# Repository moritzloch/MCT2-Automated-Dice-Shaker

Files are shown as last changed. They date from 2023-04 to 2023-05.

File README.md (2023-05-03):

# Automated Dice Shaker

***
Project for "Introduction to Microcomputers 2" by Marco Schweizer & Moritz Loch

&copy; 2023

***

## Konzept

Die Entwicklung des Konzeptes für dieses Projekt erfolgte mithilfe von ChatGPT und dem Prompt "Lustige Arduino Projekte". Die Idee eines automatisierten Würfelbechers wurde zum "Mäxle-Automat" erweitert, ein Automat der das beliebte Würfel-(Trink-)spiel spielen kann.
In der ursprünglichen Planung war angedacht, das automatisierte Würfeln durch eine rotierende Grundplatte zu realisieren. Der Würfel sollte durch den Drehimpuls gewürfelt werden. Zur Erkennung des Würfelergebnisses sollte ein Farbsensor die Farbe eines Farbwürfels registrieren.
Die folgende Skizze zeigt das ursprüngliche Konzept.

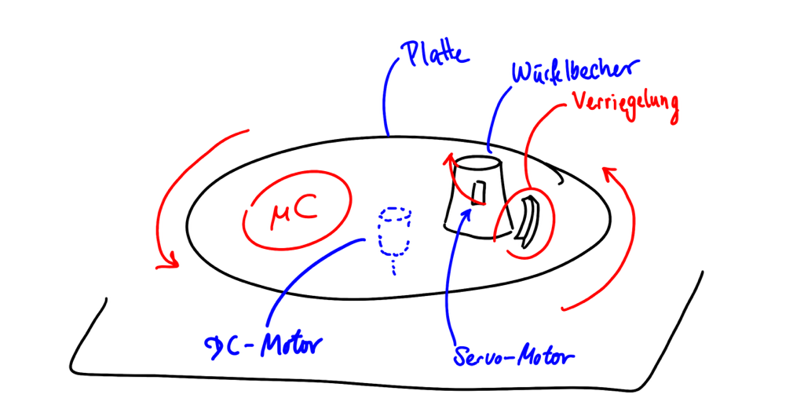
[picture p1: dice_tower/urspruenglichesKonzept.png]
Skizze des ursprüngliches Konzepts


Zu Beginn des Projektes zeigte sich, dass der TCS3200 Farbsensor nicht zuverlässig die Farbe des Farbwürfels identifizieren kann. Grund dafür ist unter anderem, dass keine gleichmäßige Belichtung des Würfels sichergestellt werden konnte und die Farben des Würfels im RGB-Farbspektrum zu nahe beieinander liegen, dass häufige Verwechslungen auftraten.
Deshalb wurde entschieden, Mäxle-Spiel und das Würfeln separat zu entwickeln. Beide Komponenten sind so aufeinander abgestimmt, dass eine zukünftige Zusammenführung problemlos ist. Für die notwendige Schnittstelle dazwischen, ist in Zukunft ein anderer Sensor zu Betrachten.

***

## Mäxle-Spiel

### Aufbau

Die Software zum Mäxle-Spiel umfasst eine Finite State Machine (FSM) mit 26 Zustände. Diese ermöglicht eine umfangreiche Menüsteuerung, sowie die Konfiguration und Durchführung von drei verschiedene Spielmodi. Die Informationsausgabe erfolgt mit einem 16x2 LCD-Display. Der Spieler kann durch Drehung eines Rotary Encoders Werte auswählen. Zustandsübergänge geschehen bei Knopfdruck des Rotary Encoders. Ein weiterer Knopf setzt den Zustandsautomaten zurück.
Beide Knöpfe sind Interruptgesteuert.
Die Hauptbedienelemente wurden zur komfortableren Handhabung in ein Bedientableau eingebettet.

### Programmablauf

Im Setup werden das LCD-Display initiiert, I/O deklariert und Interrupts angehängt. Außerdem werden die Menüs und Spieldaten zurückgesetzt.
Die Schleife fragt periodisch ab, ob eine der Interrupt-Flaggen gesetzt wurde. Der Encoder-Interrupt löst einen Übergang zum nächsten Zustand aus. Der Reset-Interrupt setzt das Spiel zurück. Andernfalls wird die, zum aktuellen Zustand zugehörige, Funktion ausgeführt.

Folgende Abbildung zeigt den vereinfachten [Programmablauf](/doc//Maexle_program_sequence.pdf).

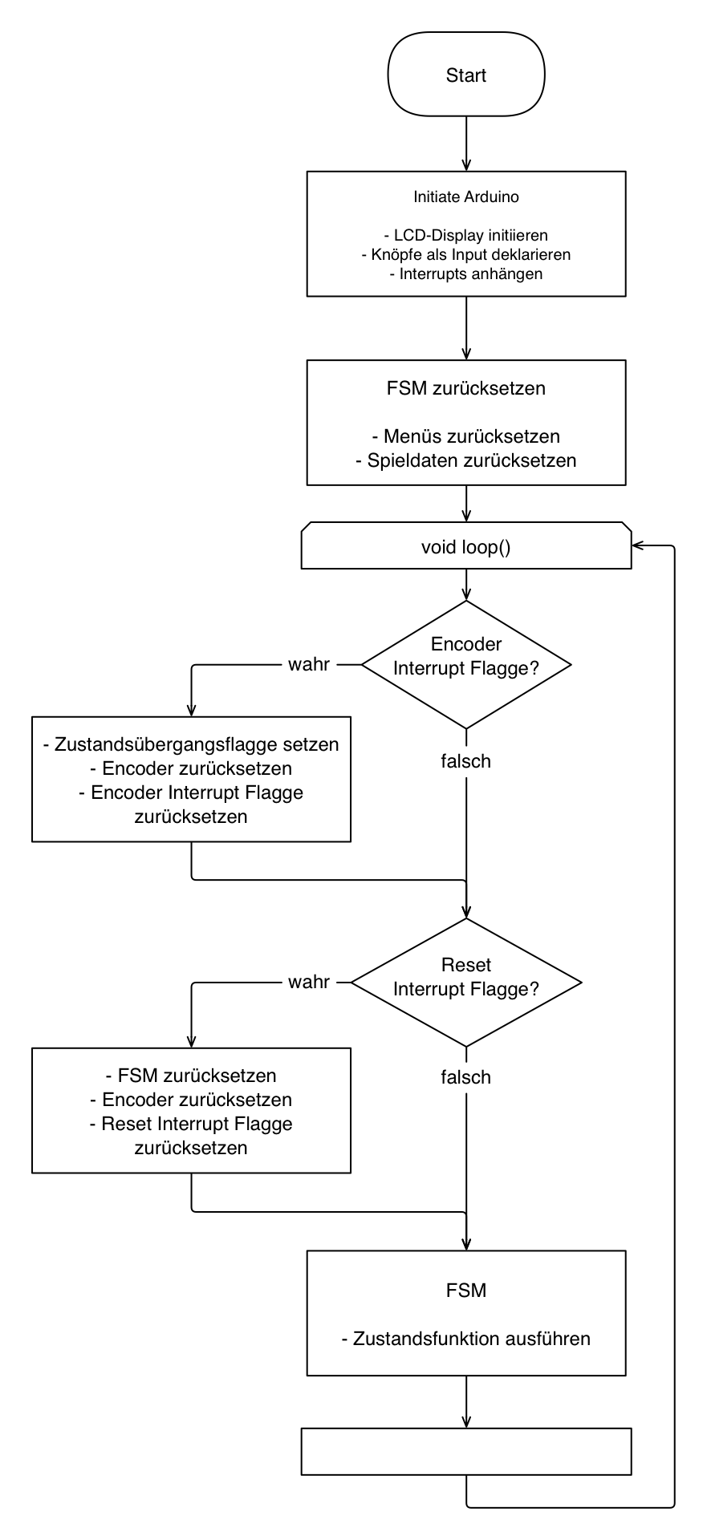
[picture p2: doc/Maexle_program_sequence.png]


### Zustandsautomat

Der Zustandsautomat ist durch ein Switch-Case-Statement implementiert. Dabei besitzt jeder Zustand eine eigene Funktion. In dieser ist sowohl die auszuführende Aktivität als auch der Übergang zum nächsten Zustand geregelt.

Ausgangspunkt des Programms bildet das Hauptmenü zur Auswahl der Spielmodi. Dieses und alle weiteren Scroll-Menüs sind als Funktion implementiert. Diese ermöglicht die Darstellung eines beliebigen Scroll-Menüs. Auch alle weiteren Displayausgaben sind als allgemeine Funktionen umgesetzt.

```c
/**
 * @brief Custom scroll selection menu on lcd display
 * 
 * @param menuProperties Menu from which the items will be selected
 * @param menuItemNames Names of the items in the menu
 * @param firstFrame First frame of FSM state flag
 * @return uint8_t 0
 */
uint8_t lcdScrollMenu(MenuProperties* menuProperties, const char** menuItemNames, bool* firstFrame)
```

Vom Hauptmenü aus gelangt der Spieler in die Nebenspielmodi "Würfeln" und "Noten würfeln". Beide können durch Einstellung der Würfel- und Augenzahl bzw. der maximalen Bestnote beliebig konfiguriert werden. Alle Spieleinstellungen und -daten werden in der folgenden Struktur gespeichert.

```c
/**
 * @brief Stores all current data of FSM
 * 
 */
struct FsmProperties{
    bool stateTransition = false;
    bool firstFrame = true;
    state_t currentState = ST_MENU;
    state_t nextState = ST_MENU;
    gameMode_t gameMode;

    int8_t numberOfLives;
    int8_t numberOfPlayers;
    uint8_t lifeCount[9];
    uint8_t currentPlayer;
    uint8_t nextPlayer;
    int8_t prevDiceRollIndex;
    int8_t diceRollIndex;
    bool trueNumberAnnounced;
    int8_t winningPlayer = -1;

    int8_t numberOfDice;
    int8_t numberOfEyes;

    float maxGrade = DEFAULTMAXGRADE;

    bool autoDiceRoll = DEFAULTAUTODICEROLL;
  };
  static FsmProperties fsm;
  ````

Anschließend liefert das Programm mit jedem Knopfdruck ein neues Würfelergebnis bzw. eine neue Note.

Bei Auswahl des Hauptspielmodus "Mäxle" kann der Spieler zunächst die Anzahl von Leben und die Anzahl der Spieler, die neben der CPU am Spiel teilnehmen wählen. Bei Spielbeginn wird zufällig ein Spieler ausgesucht, der beginnt.
Menschliche Spieler geben ihre Würfelsumme mittels Drehencoder ein. Die CPU würfelt pseudozufällig. Stattdessen kann zukünftig das automatisierte Würfeln mittels Würfelturm eingebunden werden.
Der nächste Spieler entscheidet anschließend mit einem Auswahlmenü ob er dem vorhergehenden Spieler glaubt oder nicht. Muss die CPU entscheiden, so tut sie das zufällig. Falls dem würfelnden Spieler nicht geglaubt wird muss dieser nun aufdecken, ob er tatsächlich gelogen hat. Andernfalls beginnt ein neuer Spielzug. Ist der würfelnde Spieler die CPU, dann wird dieser Schritt übersprungen. Zum Schluss wird dem lügenden oder dem falsch ratenden Spieler ein Leben abgezogen.
Ein abschließender Zustand überprüft ob das Spiel im vergangen Spielzug bereits gewonnen wurde und setzt die Spielzugdaten zurück. Falls das Spiel gewonnen wurde, wird der Sieger auf dem Display ausgegeben und das Spiel kehrt ins Hauptmenü zurück. Andernfalls beginnt der Spielzug des nächsten Spielers.

Der vollständige Zustandsautomat ist [hier](/doc/Maexle_State_Diagram.pdf) zu sehen.

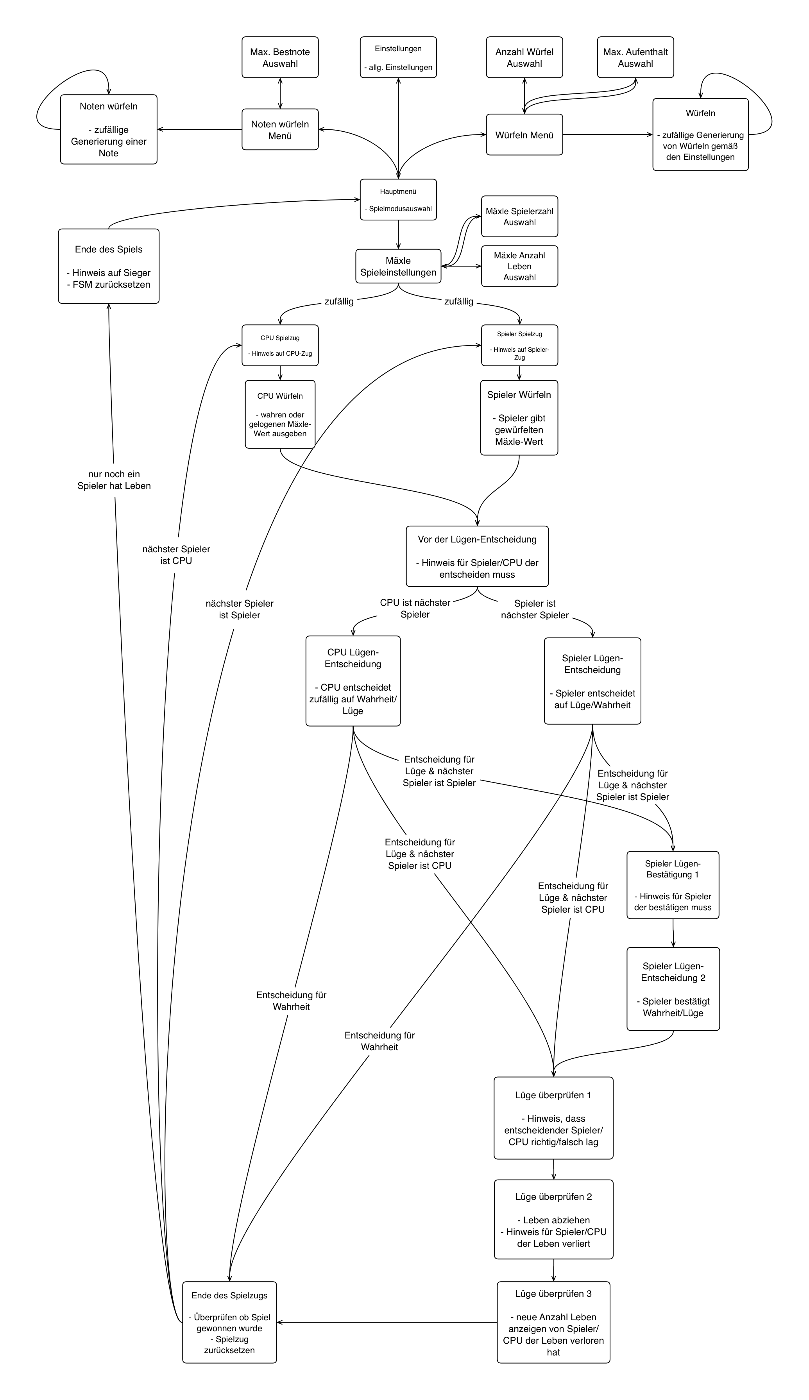
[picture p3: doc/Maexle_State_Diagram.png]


***

## Würfelturm

Neben den Bedien- und Anzeigeelementen (LCD-Display, Rotary Encoder und Taster), lag der Fokus vor allem auf dem halbautomatischem Würfelsystem.
Das ursprüngliche Konzept mit Farberkennung und rotierender Würfelfläche wurde nicht allein aufgrund des Sensors zugunsten der aktuellen Version verworfen, sondern auch bedingt einiger Probleme in der Hardware. Zum einen ist eine rotierende Platte der vorgesehenen Größe schwer zu realisieren, da der Aufbau komplex sein müsste um nicht (in anfänglichen Tests) aus der Balance zu geraten. Zum anderen sind Zweifel an der Umsetzbarkeit aufgekommen, da der Servo den Becher fest auf der Oberfläche halten soll, während die Platte mit einer hohen Drehzahl rotieren muss um den Würfel anzuheben.

Aufgrund dieser Punkte kam es zum Wechsel der Konzepte: Bestehend aus 2 Servos und einer Menge an [selbst entworfenen Bauteilen](/dice_tower/DiceShaker_Files) wurde ein System von Grund auf entwickelt, das mit einer Ausreichenden Zuverlässigkeit auf Anforderung selbstständig würfeln kann. Zukünftig kann die Ansteuerung des Mechanismus direkt durch das Programm des Mäxle-Spiels erfolgen.

Der Würfelturm besteht aus drei Bereichen: Dem Turm, dem Auffangbereich und dem Hubarm.
Der Turm besteht aus zwei schräg angeordneten Platten, welche den Würfel ablenken, wodurch dieser eine zufällige Flugbahn annimmt. Gespeißt wird er durch den Hubarm. Dieser wiederrum erhält den Würfel durch einen Servo-Motor aus dem Auffangbereich, welcher so geformt ist, dass der Würfel bei der Landung oder spätestens bei der Beförderung durch den Servo mittig platziert wird, sodass dieser stets in den Behälter am Hubarm gelangt. Durch Bauteiltoleranzen kann der Würfel quer stehen oder nicht beim ersten Mal in den Behälter passen, weshalb durch Test herausgefunden wurde, dass durch Wiederholen der Servobewegung die Zuverlässigkeit wesentlich erhöht werden konnte. Deshalb wurde dies im finalen Code implementiert.

Die Ansteuerung der Servos geschieht mit dem Arduino über die `#include <Servo.h>` Bibliothek. Bei Knopfdruck wird über die Interruptroutine eine Flag gesetzt, welche die Routine abfragt und gegebenfalls einen Würfelvorgang startet. Es wurden 2 Befehle implementiert `void stepServo(int number, int pos)` und `void jumpServo(int number, int pos)`, welche den entsprechenden Servo zu der gewünschten Position bewegen. Die Position des Servos wird schrittweise verändert durch folgende Funktion:

```c
while ( bottomServo.read() != pos ) {
        j = bottomServo.read();
        bottomServo.write(j + ((pos - j) / abs(pos - j)));  //current position +- 1
        delay(3);
      }
````

Befindet sich der Würfel im Behältnis des Hubarmes, ist dies der Verweilzustand (auch Ausgangszustand), in welcher der Spieler das Ergebnis vom Würfel ablesen kann. Der Hubarm ist so gestaltet, dass sich der Würfel mitsamt Behältnis bis zu einem Winkel von circa 150° lotrecht mitbewegt und erst kurz vor Erreichen des höchsten Punktes beginnt zu kippen, sodass der Würfel in den Turm geworfen wird.

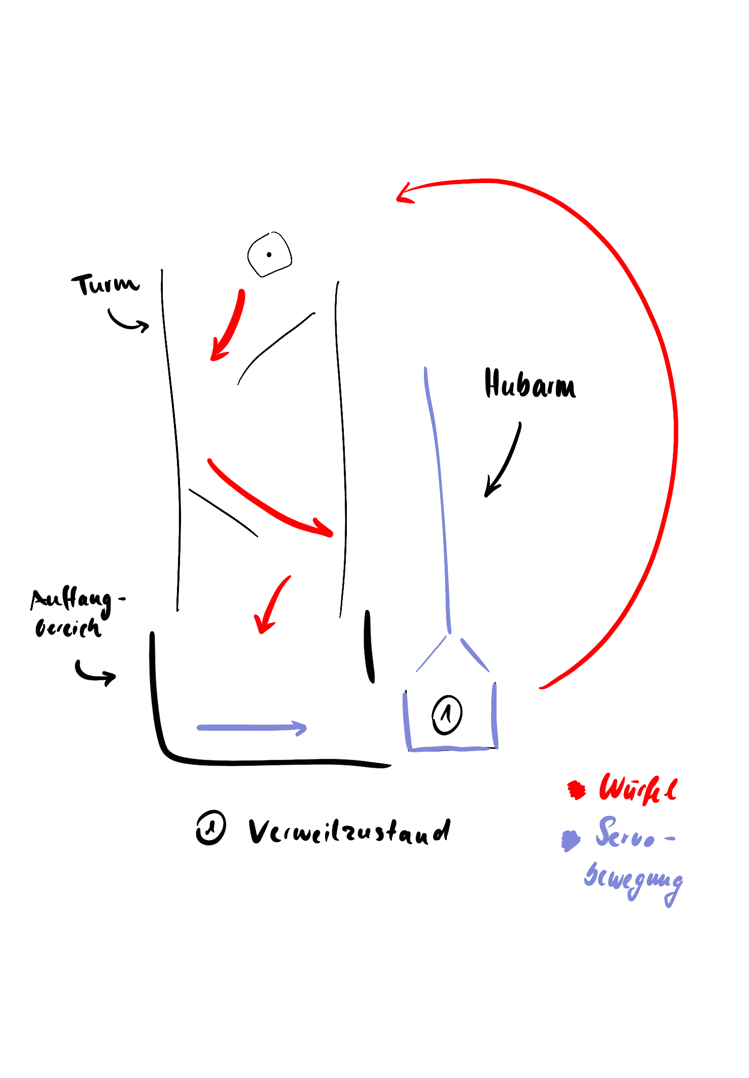
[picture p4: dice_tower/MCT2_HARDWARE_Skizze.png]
Würfelturm Skizze


***

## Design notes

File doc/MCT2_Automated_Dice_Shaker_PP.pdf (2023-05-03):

# Laborprojekt

x

# Automated Dice Shaker

### Mikrocomputertechnik II

04.05.2023

### Marco Schweizer & Moritz Loch

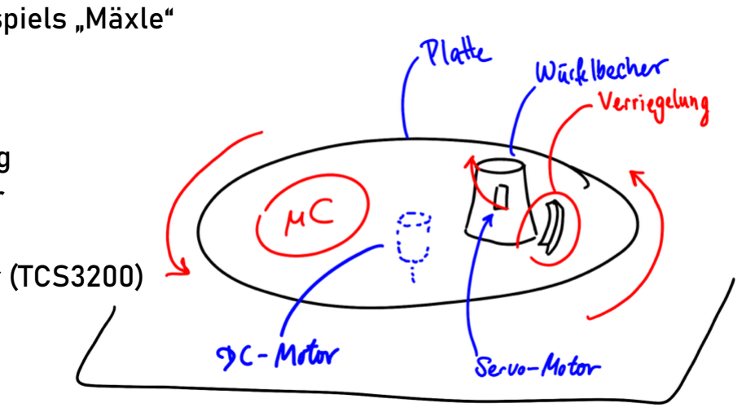
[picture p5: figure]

- Realisierung des Würfel- (Trink-)spiels „Mäxle“
- Software
- Reales Würfeln mit Farberkennung
- Rotierende Platte → DC-Motor
- Würfelbecher → Servo-Motor
- Farberkennung → Farbsensor (TCS3200)
- Anzeige und Bedienung
04.05.2023 | Automated Dice Shaker | 2

Ursprünglicher Ansatz

## Konzept

- Unzureichende Zuverlässigkeit des Sensors
- Keine gleichmäßige Belichtung
- Farben des Würfels im RGB-Farbspektrum zu nah beieinander
- Zu großer Mechanischer Aufwand, Instabilität des Aufbaus
- Änderungen:
- Trennung des Projektes in Mäxle-Spiel und Würfelturm
→ Zukünftige Schnittstelle durch alternativen Sensor
- Neues Hardware Konzept
- Keine rotierenden Elemente
- Kein Würfelbecher
→ Würfelturm mit Hub

Neuer Ansatz

# Konzept

- 16x2 LCD-Display
- Rotary-Encoder zur Eingabe
- Taster für Reset
→ Interruptgesteuert
→ eingebettet in Bedientableau

Aufbau

# Mäxle-Spiel

# Mäxle-Spiel

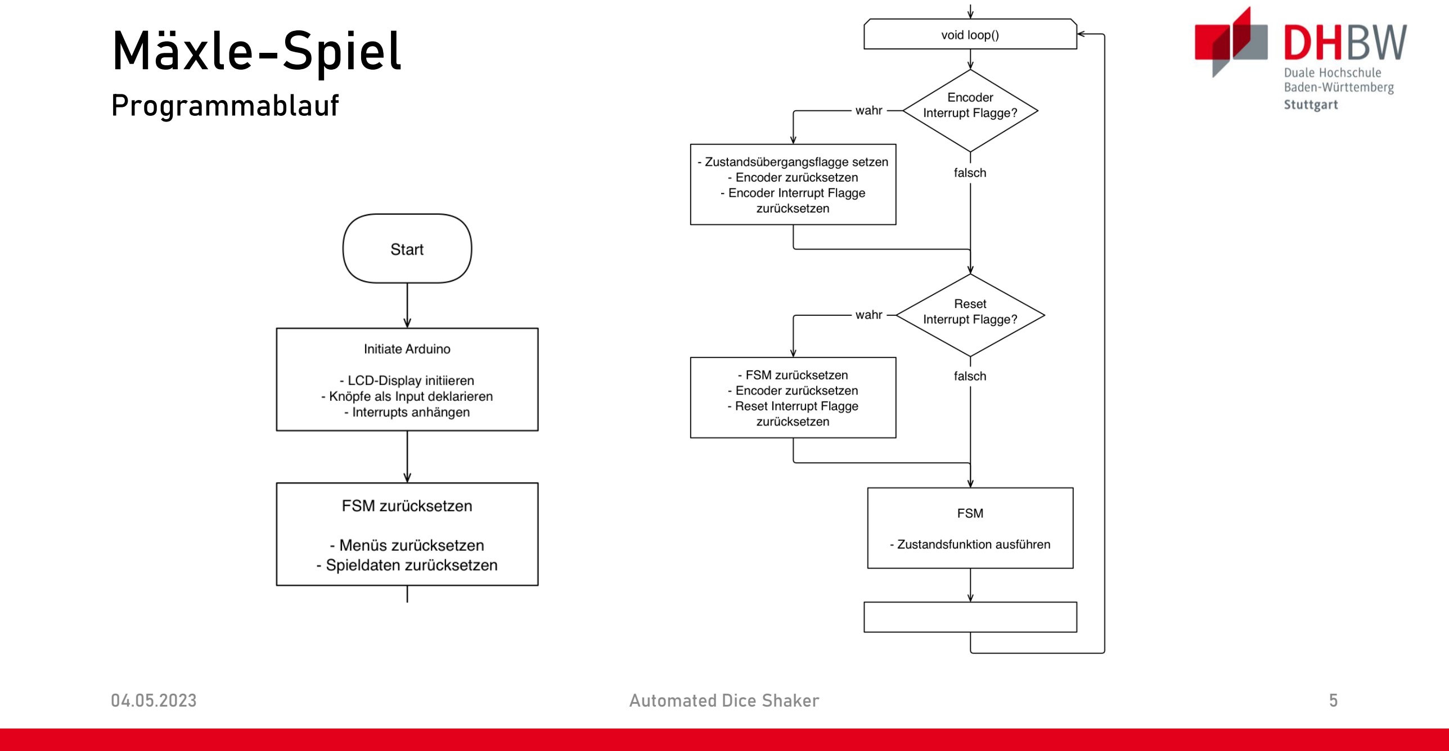
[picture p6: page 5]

Programmablauf

- 3 Spielmodi (Mäxle, Würfeln, Noten würfeln) + zukünftige Schnittstelle zum Würfelturm
- 26 Zustände
- Switch-Case Implementierung der FSM
- Eigene Funktion für jeden Zustand → Aktivität & Übergang
- Allgemeine Funktionen für LCD-Menüs, usw.
- Strukturen zum Speichern von Menülisten, Spieldaten, etc.
- State Diagram (https://github.com/moritzloch/MCT2-Automated-Dice-Shaker/blob/main/doc/Maexle_State_Diagram.pdf)

FSM

# Mäxle-Spiel

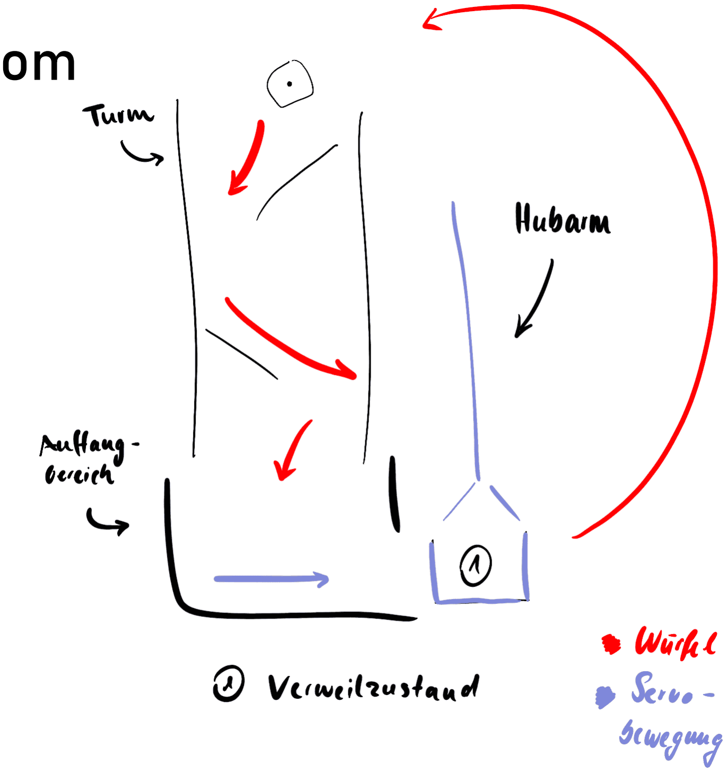
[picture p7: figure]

- separater Arduino, ggfs. Kommunikation über Pin vom Mäxle-Automat (einseitig)
- 2 Servos
- Ausgangsposition: Würfel im Korb
→ Augenzahl kann abgelesen werden
- Korb bleibt bis zu 150° lotrecht, anschließend kippt dieser und wirft den Würfel in den Turm
- Erweiterung:
- Servo um Korb zu halten
- Sensor für Augenzahl
→ vollautomatisches Spiel möglich

# Würfelturm

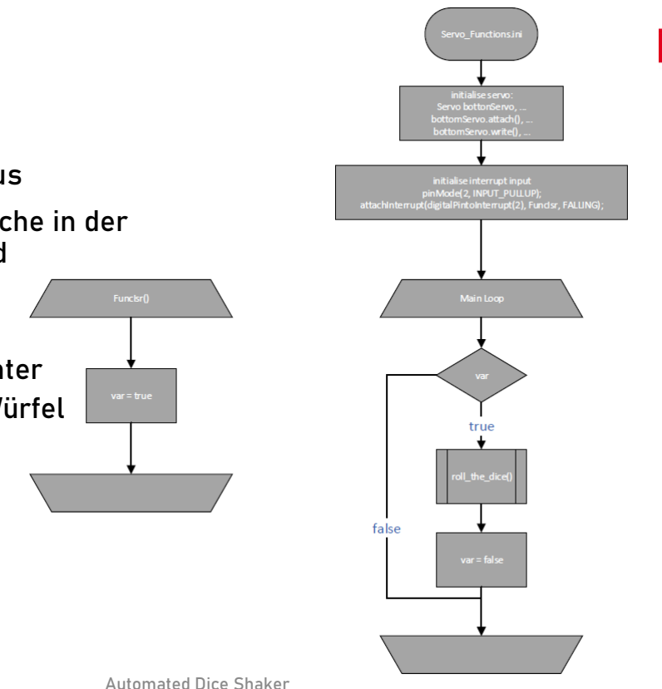
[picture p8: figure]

- Tasterdruck löst Interrupt aus
- Main Loop fragt Flag ab, welche in der Interruptroutine gesetzt wird
- Funktion wird aufgerufen:
- Hubarm fährt hoch und
anschließend wieder runter
- Unterer Servo schiebt Würfel 3 mal in Richtung des
Korbs

# Würfelturm

# Würfelturm

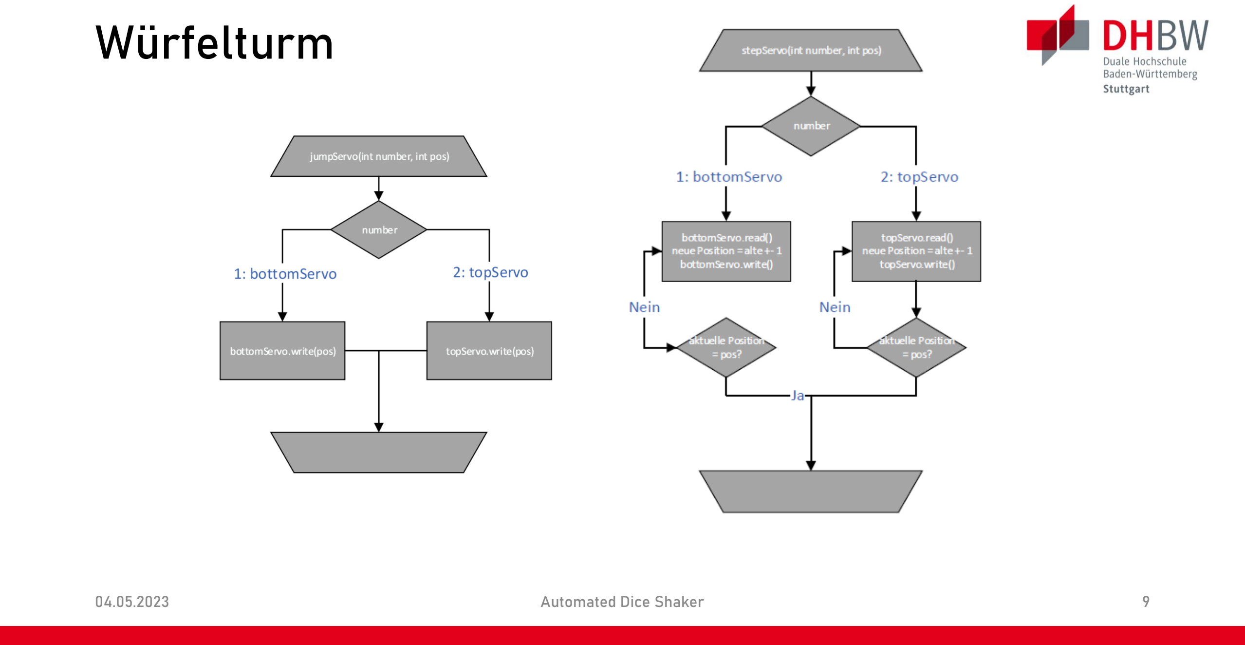
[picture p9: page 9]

# Demonstration

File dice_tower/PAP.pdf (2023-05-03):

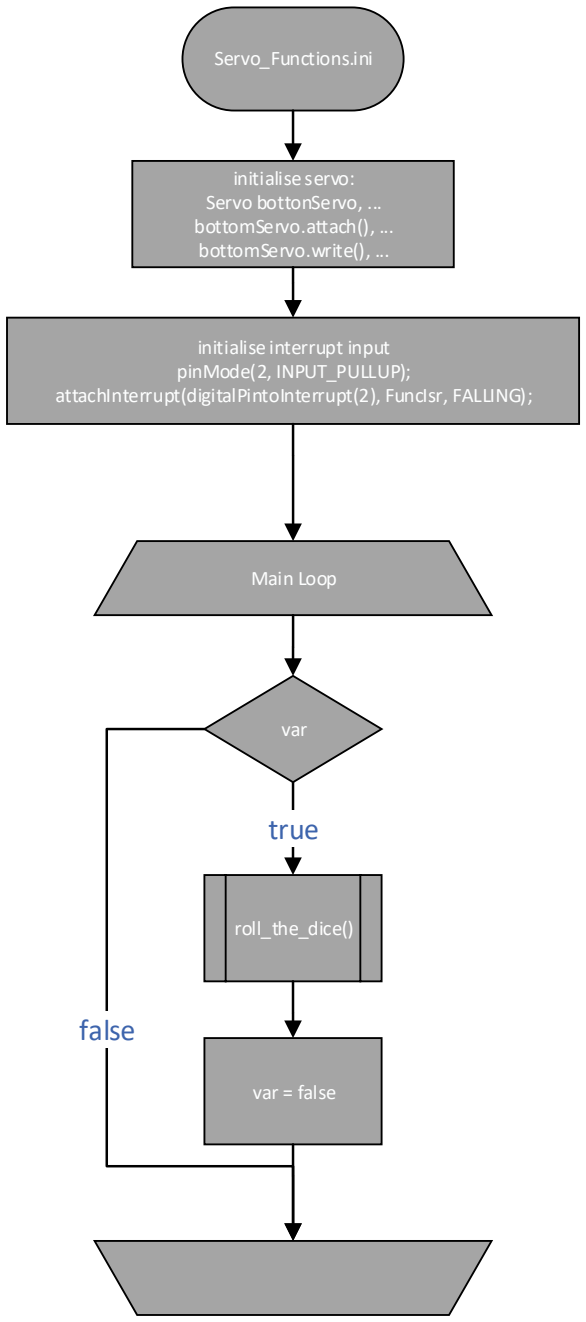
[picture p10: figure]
Servo_Functions.ini; Main Loop; var; false; roll_the_dice(); var = false; true; initialise servo: Servo bottonServo, ... bottomServo.attach(), ... bottomServo.write(), ...; initialise interrupt input pinMode(2, INPUT_PULLUP); attachInterrupt(digitalPintoInterrupt(2), FuncIsr, FALLING);

FuncIsr()

var = true

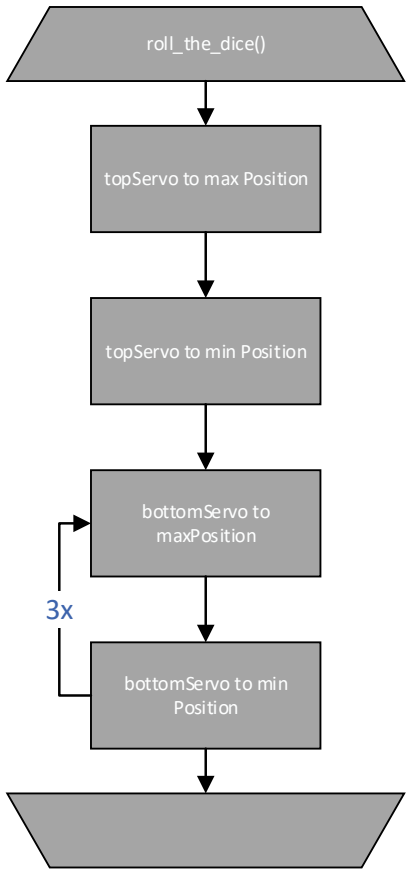
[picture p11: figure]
roll_the_dice(); topServo to max Position; topServo to min Position; bottomServo to maxPosition; bottomServo to min Position
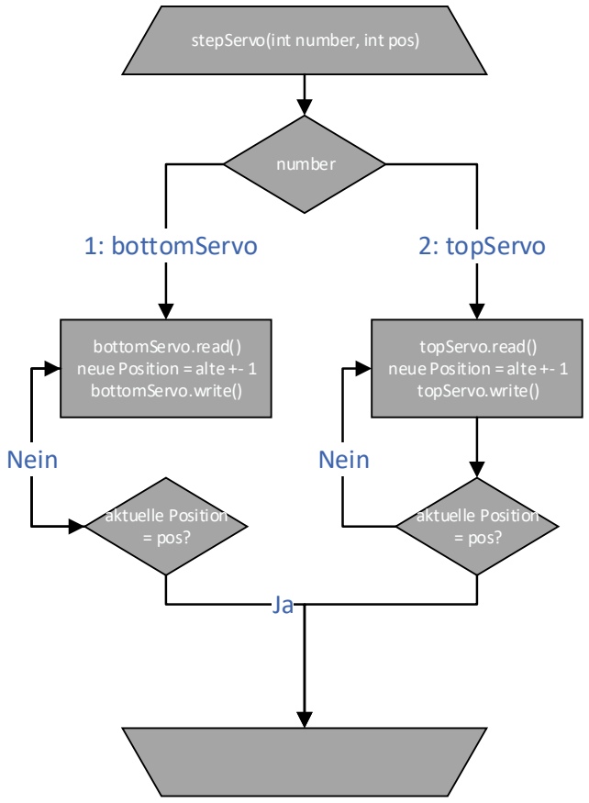
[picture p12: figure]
stepServo(int number, int pos); number; bottomServo.read() neue Position = alte +- 1 bottomServo.write(); aktuelle Position = pos?; Nein; topServo.read() neue Position = alte +- 1 topServo.write(); 1: bottomServo; 2: topServo
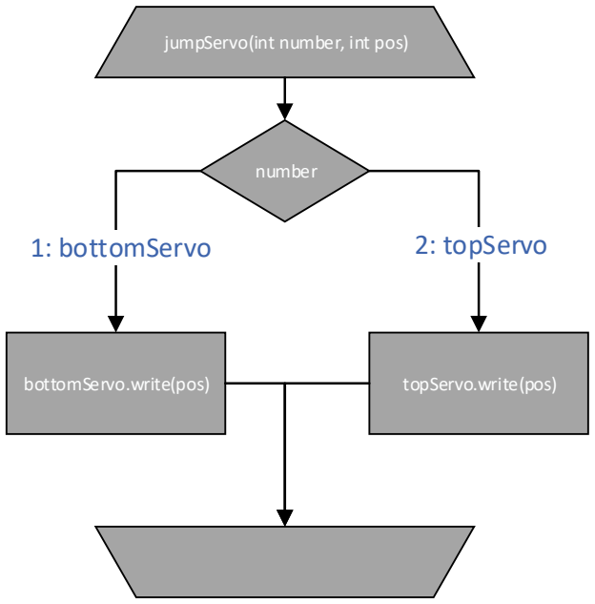
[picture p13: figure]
jumpServo(int number, int pos); number; bottomServo.write(pos); 1: bottomServo; topServo.write(pos); 2: topServo

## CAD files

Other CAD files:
dice_tower/DiceShaker_Files/Bedienfeld/Bedienfeld.ipt
dice_tower/DiceShaker_Files/Bedienfeld/Bedienfeld_Fuesse.ipt
dice_tower/DiceShaker_Files/Bedienfeld/Drehencoder.ipt
dice_tower/DiceShaker_Files/Servo Arm/Arm_Arm.ipt
dice_tower/DiceShaker_Files/Servo Arm/Arm_Boden.ipt
dice_tower/DiceShaker_Files/Servo Arm/Arm_Querstrebe.ipt
dice_tower/DiceShaker_Files/Servo Arm/Arm_Schrauben.ipt
dice_tower/DiceShaker_Files/Servo Arm/Arm_Seite.ipt
dice_tower/DiceShaker_Files/Servo Arm/ServoAdapter_oben_gewinkelt.ipt
dice_tower/DiceShaker_Files/Servo Arm/ServoAdapter_oben_kurz.ipt
dice_tower/DiceShaker_Files/Servo Arm/ServoHalterung_oben.ipt
dice_tower/DiceShaker_Files/Servo Arm/ServoHalterung_unten.ipt
dice_tower/DiceShaker_Files/Turm/Außenwand_Turm_mit.ipt
dice_tower/DiceShaker_Files/Turm/Außenwand_Turm_ohne.ipt
dice_tower/DiceShaker_Files/Turm/Turm Halterung.ipt
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

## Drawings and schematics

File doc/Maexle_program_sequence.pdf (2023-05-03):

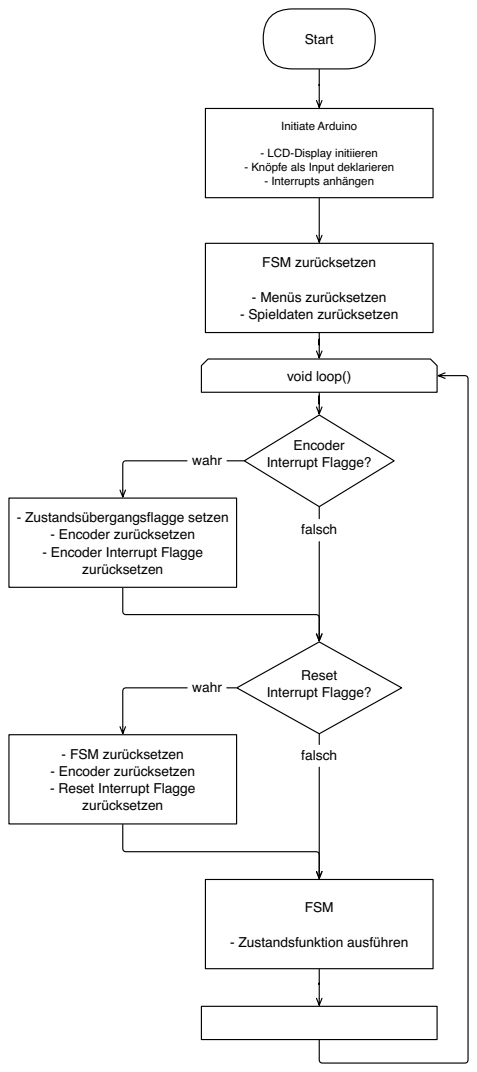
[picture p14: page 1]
wahr; falsch; Start; Initiate Arduino; FSM zurücksetzen; - Menüs zurücksetzen - Spieldaten zurücksetzen; void loop(); Encoder Interrupt Flagge?; Reset Interrupt Flagge?; FSM; - Zustandsfunktion ausführen

- LCD-Display initiieren
- Knöpfe als Input deklarieren
- Interrupts anhängen

- Zustandsübergangsflagge setzen
- Encoder zurücksetzen
- Encoder Interrupt Flagge
zurücksetzen

- FSM zurücksetzen
- Reset Interrupt Flagge

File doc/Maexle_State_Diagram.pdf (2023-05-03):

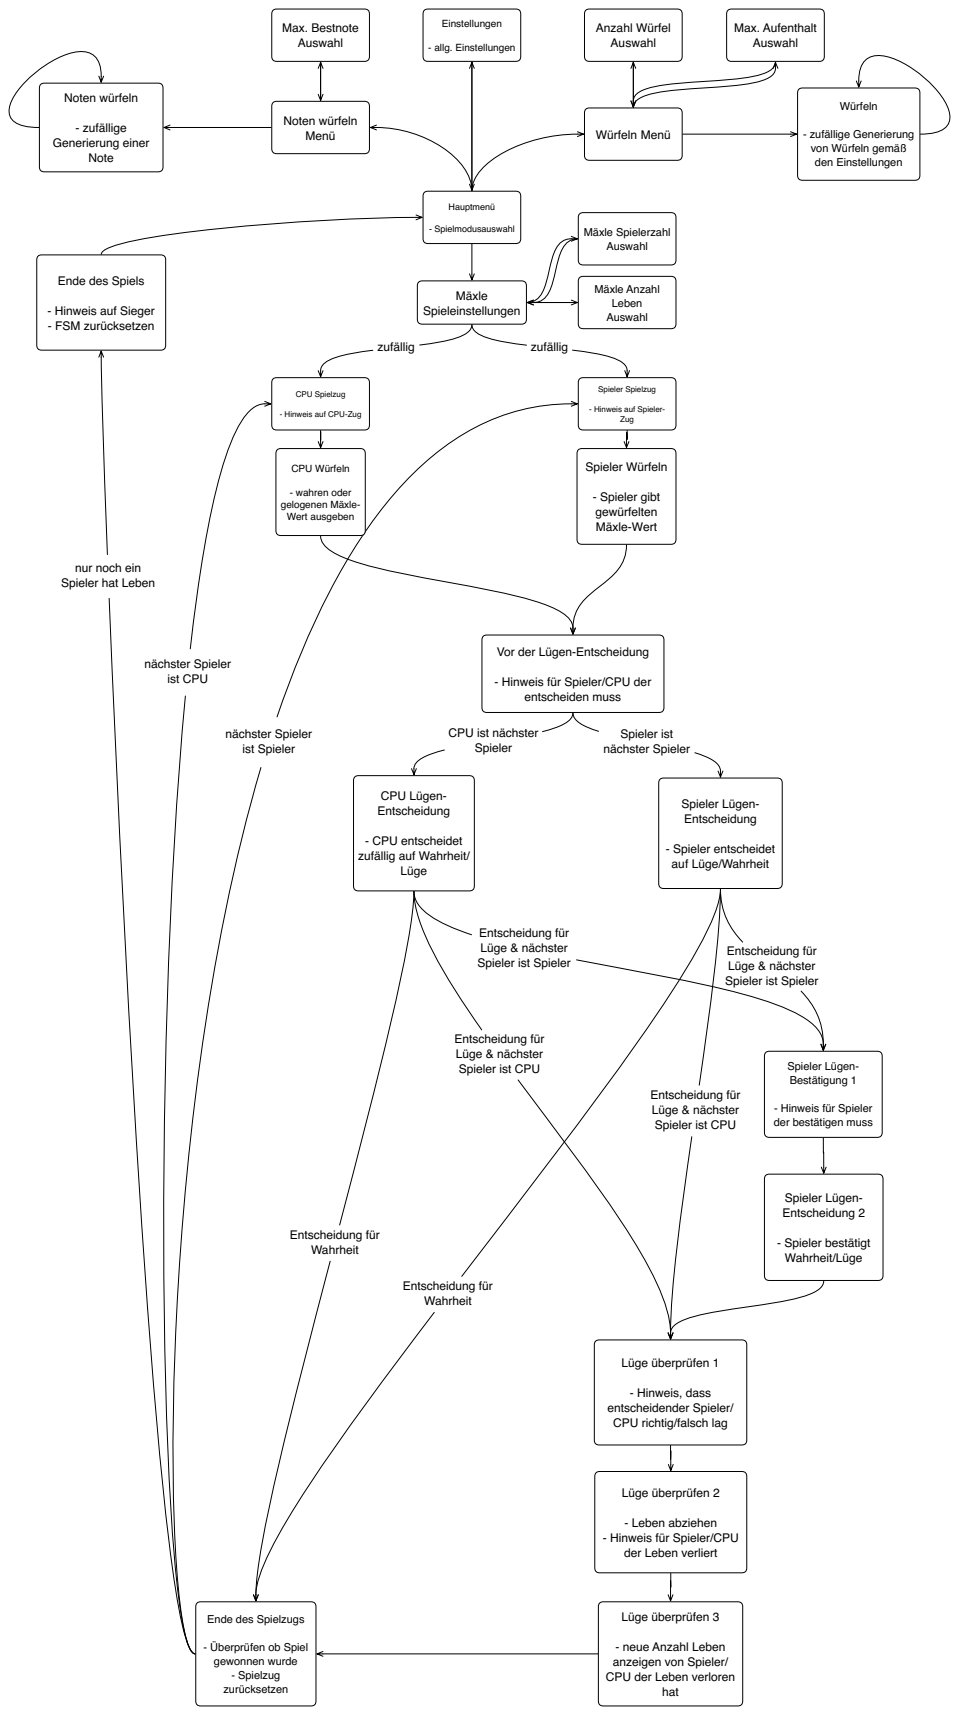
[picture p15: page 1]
zufällig; Entscheidung für Wahrheit; Spieler ist nächster Spieler; nächster Spieler ist CPU; nächster Spieler ist Spieler; Hauptmenü; - Spielmodusauswahl; Einstellungen; - allg. Einstellungen; Noten würfeln Menü; Mäxle Spieleinstellungen; Mäxle Anzahl Leben Auswahl; CPU Spielzug; CPU Lügen- Entscheidung; Lüge; Spieler Spielzug; Zug; Spieler Würfeln; - Spieler gibt gewürfelten Mäxle-Wert; Spieler Lügen- Entscheidung; Spieler Lügen- Bestätigung 1; Spieler Lügen- Entscheidung 2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

- zufällige Generierung
von Würfeln gemäß
den Einstellungen

Ende des Spiels

- Hinweis auf Sieger
- FSM zurücksetzen

- Hinweis auf Spieler-

- Hinweis auf CPU-Zug

nur noch ein
Spieler hat Leben

Vor der Lügen-Entscheidung

- Hinweis für Spieler/CPU der
entscheiden muss

CPU ist nächster
Spieler

- CPU entscheidet
zufällig auf Wahrheit/

- Spieler entscheidet
auf Lüge/Wahrheit

Entscheidung für
Lüge & nächster
Spieler ist Spieler

Spieler ist CPU

- Hinweis für Spieler
der bestätigen muss

- Hinweis, dass
entscheidender Spieler/
CPU richtig/falsch lag

- Leben abziehen
- Hinweis für Spieler/CPU
der Leben verliert

Ende des Spielzugs

- Überprüfen ob Spiel
gewonnen wurde
- Spielzug
zurücksetzen

- neue Anzahl Leben
anzeigen von Spieler/
CPU der Leben verloren

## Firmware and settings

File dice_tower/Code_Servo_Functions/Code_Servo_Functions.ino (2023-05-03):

#include <Servo.h>

Servo bottomServo;    // Servo to push dice into car
Servo topServo;       // Servo to lift dice into tower

bool var = false;

void setup() {
  /*  Call interrupt func if button on pin 2 is pressed */
  pinMode(2, INPUT_PULLUP);
  pinMode(10, INPUT);
  attachInterrupt(digitalPinToInterrupt(2), FuncIsr, FALLING);

  /*  Attach servos to pin 8 and 9*/
  bottomServo.attach(8);
  topServo.attach(9);

  /*  Move servos to initial position */
  stepServo(1, 160);                                      
  stepServo(2, 175);                                      
}

void loop() {
  if (var) {
    roll_the_dice();
    var = false;
  }
}

void roll_the_dice() {
  /* Dice needs to be placed in car
   * Lift the dice and throw into tower
   * to roll the dice */
  stepServo(2, 0);
  delay(1000);
  jumpServo(2, 130);
  delay(200);
  stepServo(2, 175);


  /* Eject the lower servo three times
   * to ensure the dice is placed in the car */
  jumpServo(2, 180);    //place car closer to outlet

  stepServo(1, 90);     //extend #1
  delay(500);
  stepServo(1, 130);
  delay(200);
  stepServo(1, 90);    //extend #2
  delay(200);
  stepServo(1, 130);
  delay(200);
  stepServo(1, 90);    //extend #3
  stepServo(2, 175);
  delay(200);
  stepServo(1, 160);
  delay(1200);
}

void stepServo(int number, int pos) 
/* Servo no.1 = bottomServo
 * Servo no.2 = topServo
 * Increase/Decrease angle of servo slowly */
{
  int j;
  switch (number) {
    case 1:
      while ( bottomServo.read() != pos ) {
        j = bottomServo.read();
        bottomServo.write(j + ((pos - j) / abs(pos - j)));  //current position +- 1
        delay(3);
      }
      break;
    case 2:
      while ( topServo.read() != pos ) {
        j = topServo.read();
        topServo.write(j + ((pos - j) / abs(pos - j)));     //current position +- 1
        delay(4);
      }
      break;
  }
}

void jumpServo(int number, int pos) 
/* Servo no.1 = bottomServo
 * Servo no.2 = topServo
 * Jump to angle */
{                 
  if (number == 1) bottomServo.write(pos);
  else topServo.write(pos);
  delay(100);
}

void FuncIsr() 
/* Interrupt Service Routine */
{
  var = true;
}

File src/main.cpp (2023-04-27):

/**
 * @file main.cpp
 * @author Marco Schweizer, Moritz Loch
 * @brief Automated Dice Shaker
 * @version 1.0
 * @date 2023-04-27
 * 
 * @copyright Copyright (c) 2023
 * 
 */

#include <stdint.h>
#include <Arduino.h>
#include <MD_TCS230.h>
#include <Encoder.h>

#include "config.h"
#include "tcsFunctions.h"
#include "basicFunctions.h"
#include "menuFunctions.h"
#include "gameStateFunctions.h"


void setup(){

  initArduino();
  resetFSM(&fsm, menus);

}

void loop(){

  /**
   * @brief Encoder button press
   * 
   */
  if(encoderInterrupt){
    (&fsm)->stateTransition = true;
    (&fsm)->firstFrame = true;
    resetEncoder();
    delay(250);
    encoderInterrupt = false;
  }

  /**
   * @brief Reset button press
   * 
   */
  if(resetInterrupt){
    resetFSM(&fsm, menus);
    resetEncoder();
    delay(250);
    resetInterrupt = false;
  }

  /**
   * @brief Finite State Machine
   * 
   */
  gameStateFSM(&fsm, menus);

}


void encoderPressed(){
  encoderInterrupt = true;
}

void resetPressed(){
  resetInterrupt = true;
}

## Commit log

2023-04-02 Added library for TCS3200 colour sensor
2023-04-02 Changed controller from Arduino Uno to Mega
2023-04-02 Added pins in config.h for RGB LED
2023-04-02 Initial commit of Color Sensing and Visualising
    This branch contains all functions and ain code for reading color with the TCS3200 color sensor and visualising the color with an RGB LED.
2023-04-21 Added LCD-Display and Rotary Encoder for user interaction
2023-04-22 Added ISR for Encoder button press for state transitions
2023-05-02 Added powerpoint
2023-05-02 Added inventor files
    [45°Winkel_klein.ipt, Arm_Arm.ipt, Arm_Boden.ipt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]
2023-05-03 Add flowchart
